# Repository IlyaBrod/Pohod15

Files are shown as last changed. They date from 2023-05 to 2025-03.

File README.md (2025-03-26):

<div align="center">
<table border="0">
 <tr>
    <td><h1> Pohod15Leg </h1>
    CAD views of the Pohod15 bio-inspired leg. (1) DC motor (2) Angle (3) Force sensor (4) Worm gear (5) Spur gear (6) Control circuit (7) Silicone tip.<br><br>  
      <div align="center">
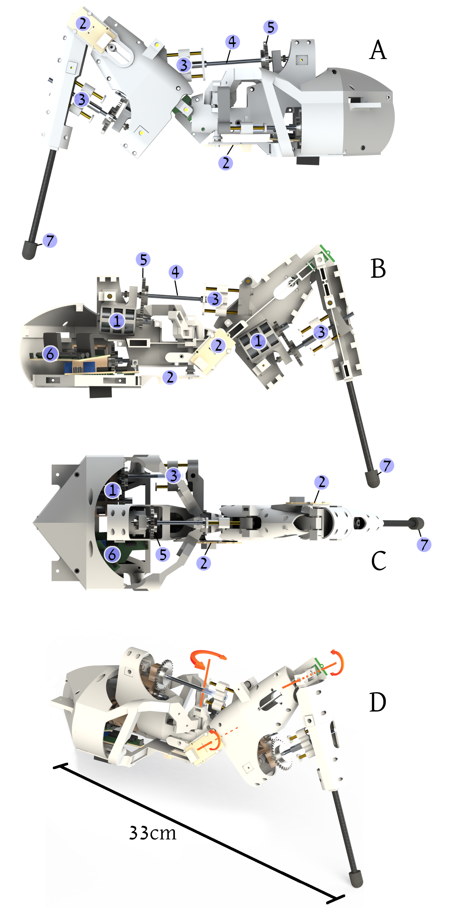
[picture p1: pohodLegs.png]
      
    </div>
    </td>
    <td>
    <h1> Description: </h1>
    This project presents the design of a 3 DoF bio-inspired robotic leg. The desert ant <i>Cataglyphis fortis</i> was used as a reference for segment sizing, with a scale ratio of 1:30.<br><br>
The structure is mainly composed of FDM 3D-printed parts. An additional carbon fiber shaft is used for the tibia, and a silicone molded tip improves surface adherence.<br>  
The actuation system consists of 3 DC motors (MABUCHI RK-370CC-14230), controlled with a custom-built shield made of L298N. However, nowadays, there are good Pololu control boards available (<a href="https://www.pololu.com/category/10/brushed-dc-motor-controllers">Pololu control boards</a>).<br>  
An irreversible worm-gear system is built using custom-machined axes jointed to Delrin spur gears to double the motor's torque output. These parts can also be assembled from cut threaded rods.<br>  
Angular sensors are based on the AS5600 from AMS OSRAM manufacturer. <br><br>
    <h1>  Files: </h1>
    <h3>./Pohod15ExoC</h3>
              CAD assembly files for Solidworks. An aditional .STEP model is provided.
    <h3>./ActuatorControl</h3>
              Provide the STM32 code, for actuator position control, 3DoF leg inverse kinematics and trajectory generation.  <br><br>
              The projet was configured using STM32CubeMX software (NUCLEO STM32F411RE setup). We suggest to use STM32Studio for the code developpment.   
    <h3>./Joint sizing  </h3> 
              Provide a graphical software to choose manually the optimum size of the irreversible joint, depending the desired output torque.
    </td>
 </tr>
</table>
</div>
  
## Want to learn more about hexapod robotics?  
- Brodoline, I., Sauvageot, E., Viollet, S., Serres J. R., Shaping the energy curves of a servomotor-based hexapod robot. Sci Rep 14, 11675 (2024).
  <a href="https://doi.org/10.1038/s41598-024-62184-y">https://www.nature.com/articles/s41598-024-62184-y</a>
- Manoonpong P, Patanè L, Xiong X, Brodoline I, Dupeyroux J, Viollet S, Arena P, Serres JR. Insect-Inspired Robots: Bridging Biological and Artificial Systems. Sensors. 2021; 21(22):7609.
<a href="https://www.mdpi.com/1424-8220/21/22/7609">https://doi.org/10.3390/s21227609</a>

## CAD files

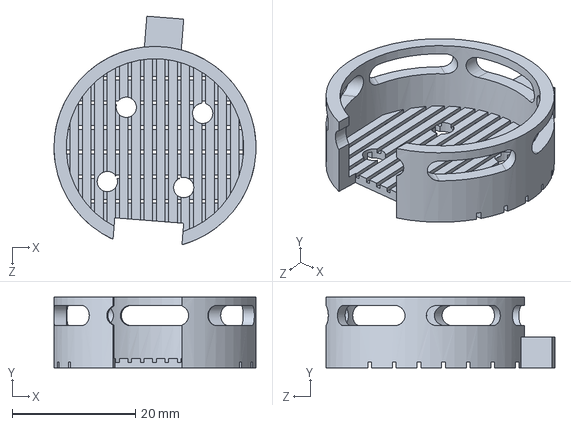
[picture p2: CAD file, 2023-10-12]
Pohod15ExoC/electronics/motor_IQ_attach.SLDPRT
32.7 x 11.5 x 37.1 mm

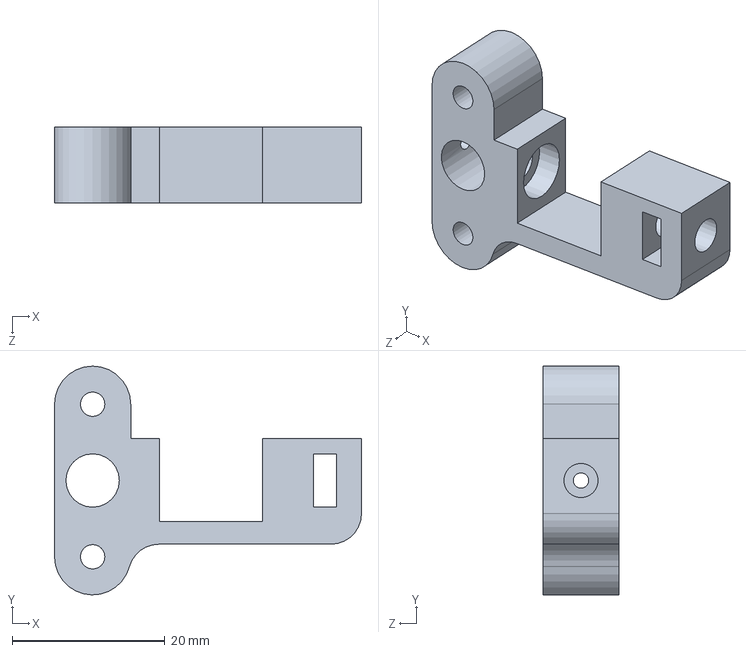
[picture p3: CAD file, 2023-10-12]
Pohod15ExoC/force sensor/forceSensor_Joint_torax.SLDPRT
40.2 x 30.0 x 10.0 mm

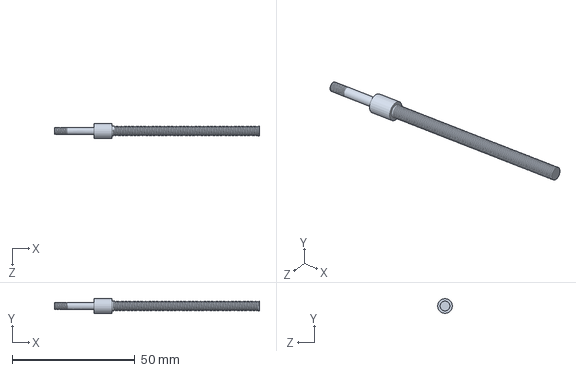
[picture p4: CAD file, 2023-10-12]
Pohod15ExoC/gears/Tibia_wormGearM4.SLDPRT
83.5 x 6.00 x 6.00 mm

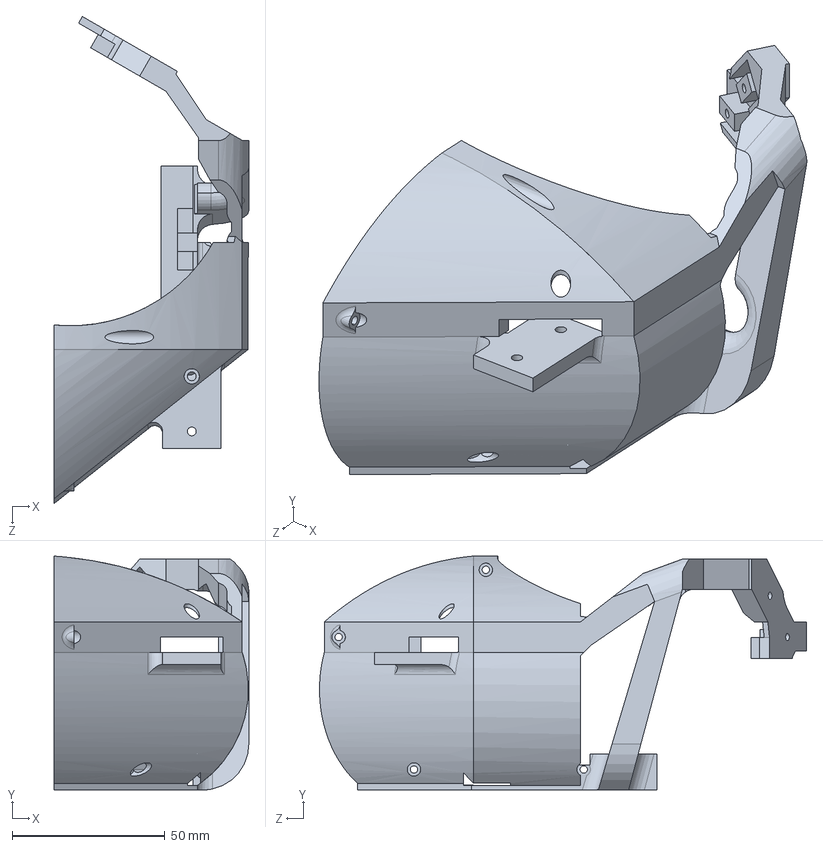
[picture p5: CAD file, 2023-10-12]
Pohod15ExoC/main parts/Symétrietorax_cuticule_R.SLDPRT
63.7 x 76.5 x 159.3 mm

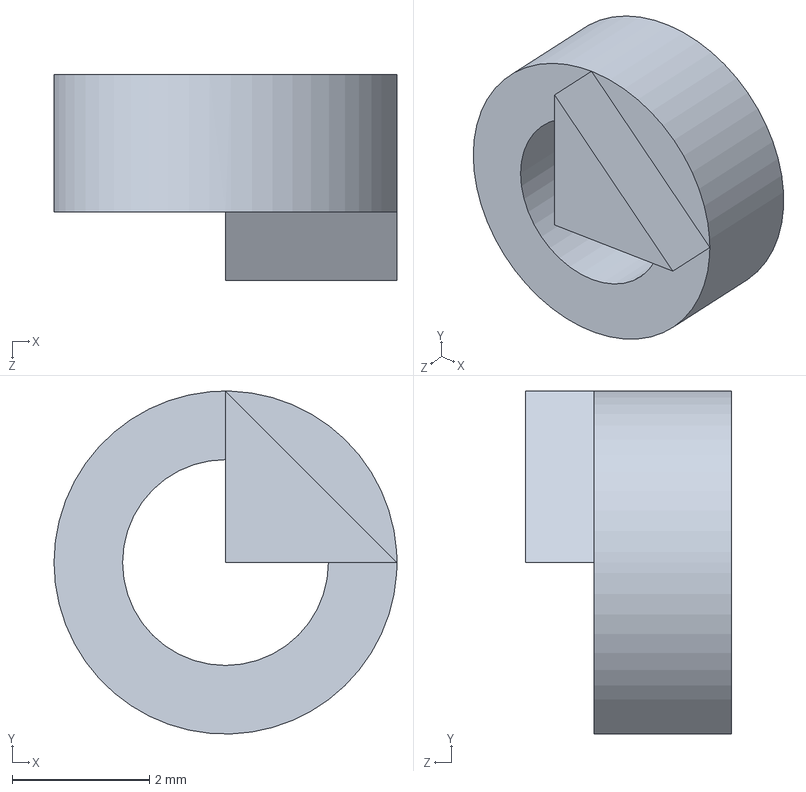
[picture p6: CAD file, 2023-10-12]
Pohod15ExoC/referenceCircle.SLDPRT
5.00 x 5.00 x 3.00 mm

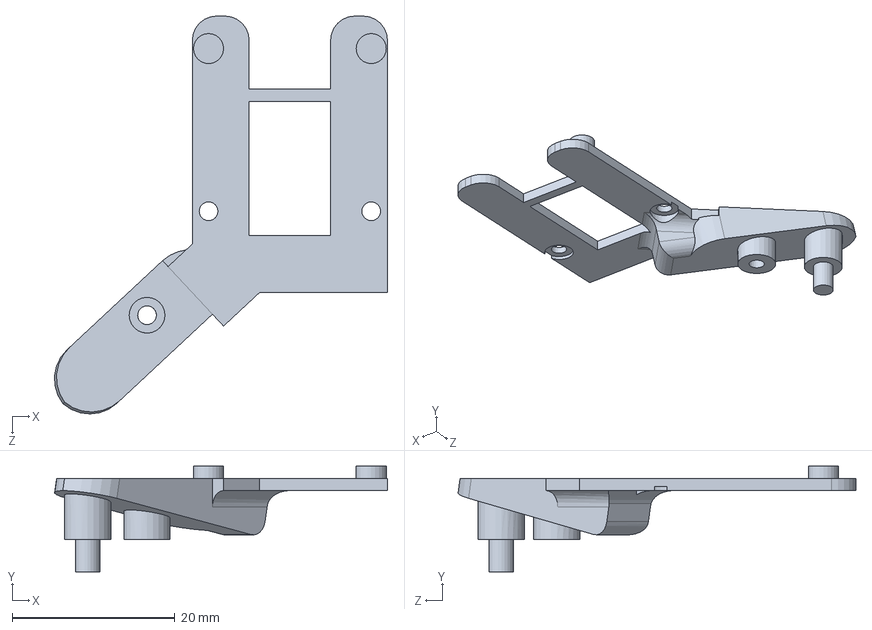
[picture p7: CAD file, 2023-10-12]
Pohod15ExoC/electronics/AS5600sensor_support_coxa.SLDPRT
40.9 x 13.0 x 48.9 mm

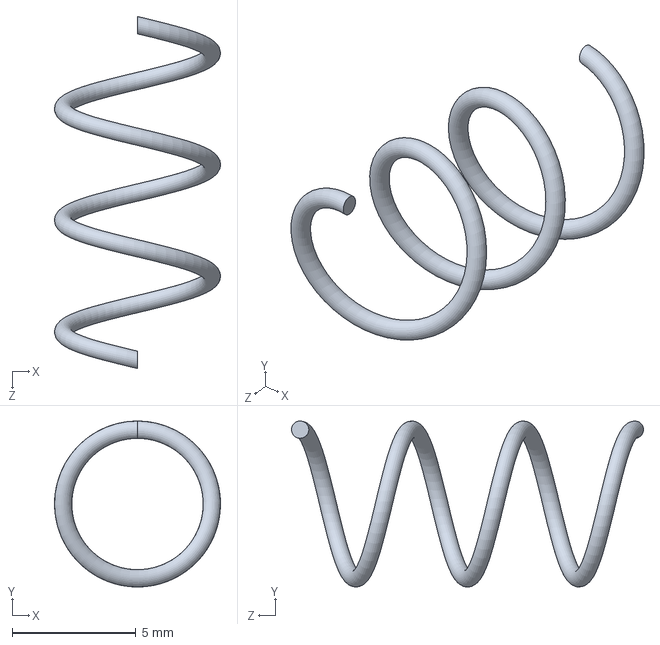
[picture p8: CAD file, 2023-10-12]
Pohod15ExoC/force sensor/forceSensor_spring.SLDPRT
6.70 x 6.70 x 14.2 mm

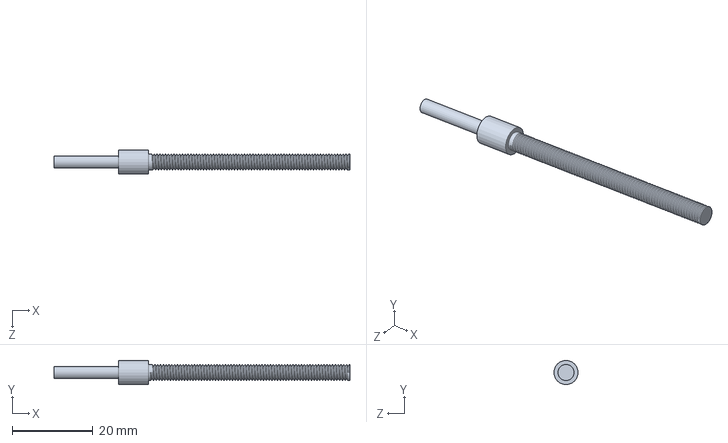
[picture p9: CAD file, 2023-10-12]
Pohod15ExoC/gears/Femur_wormGearM4.SLDPRT
73.5 x 6.00 x 6.00 mm

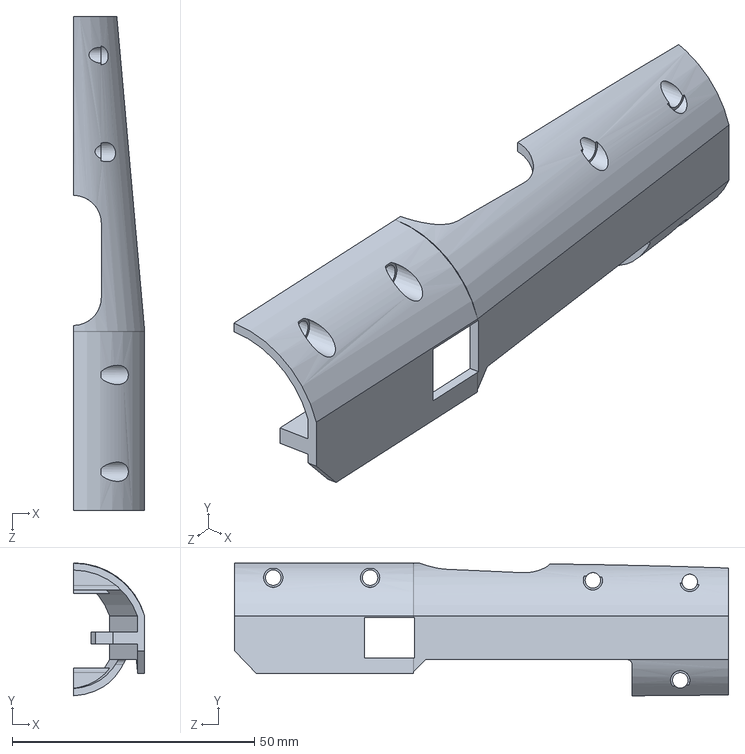
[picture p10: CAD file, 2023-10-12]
Pohod15ExoC/main parts/Symétrietibia_cuticule_R.SLDPRT
14.8 x 27.4 x 102.0 mm

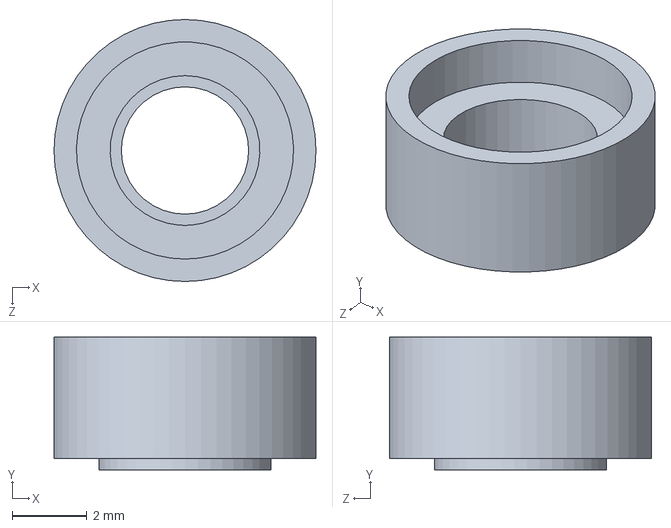
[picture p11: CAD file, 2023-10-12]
Pohod15ExoC/electronics/motor_entretoise.SLDPRT
7.00 x 3.55 x 7.00 mm

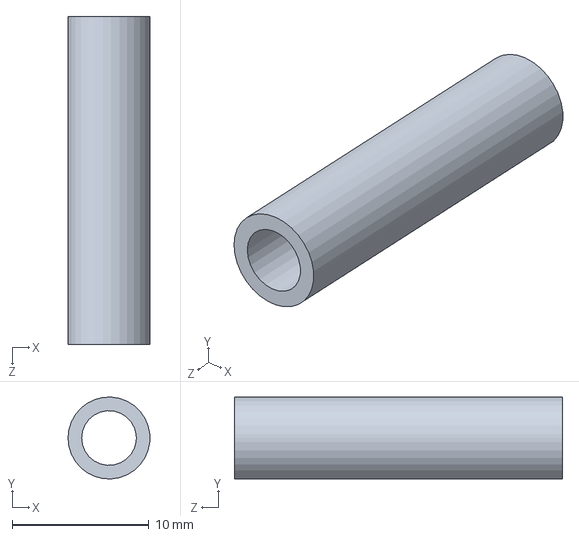
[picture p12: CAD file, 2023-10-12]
Pohod15ExoC/force sensor/forceSensor_gear.SLDPRT
6.00 x 5.99 x 24.0 mm

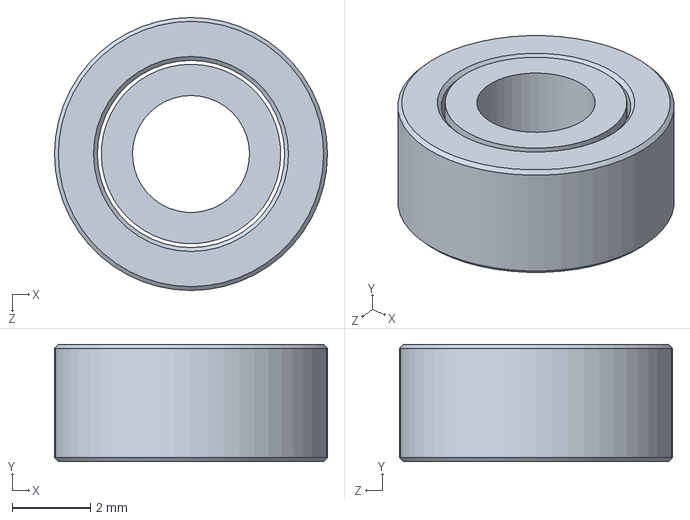
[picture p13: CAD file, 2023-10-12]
Pohod15ExoC/gears/bearing_MR63ZZ.SLDPRT
7.00 x 3.00 x 7.00 mm

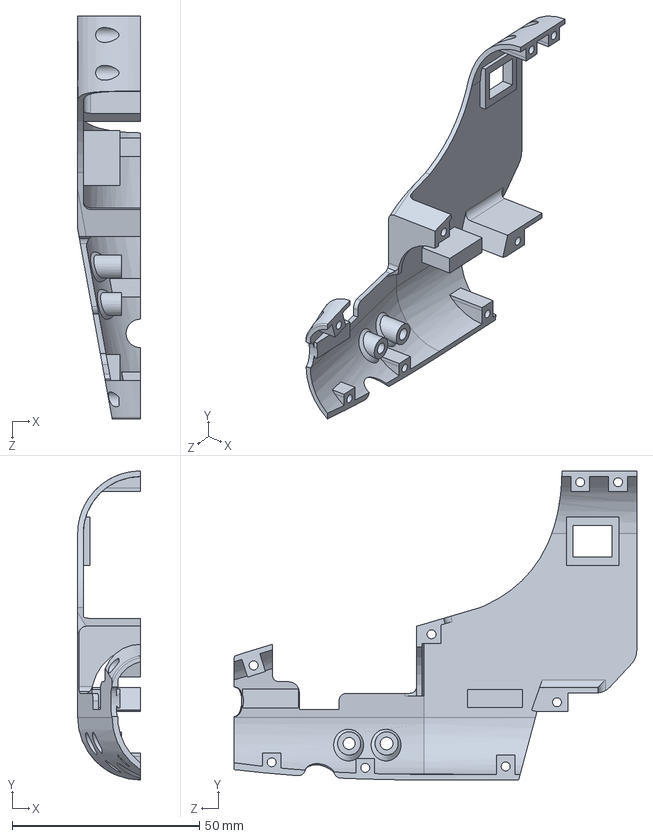
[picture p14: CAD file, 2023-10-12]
Pohod15ExoC/main parts/coxa_cuticule_R.SLDPRT
16.8 x 82.5 x 107.5 mm

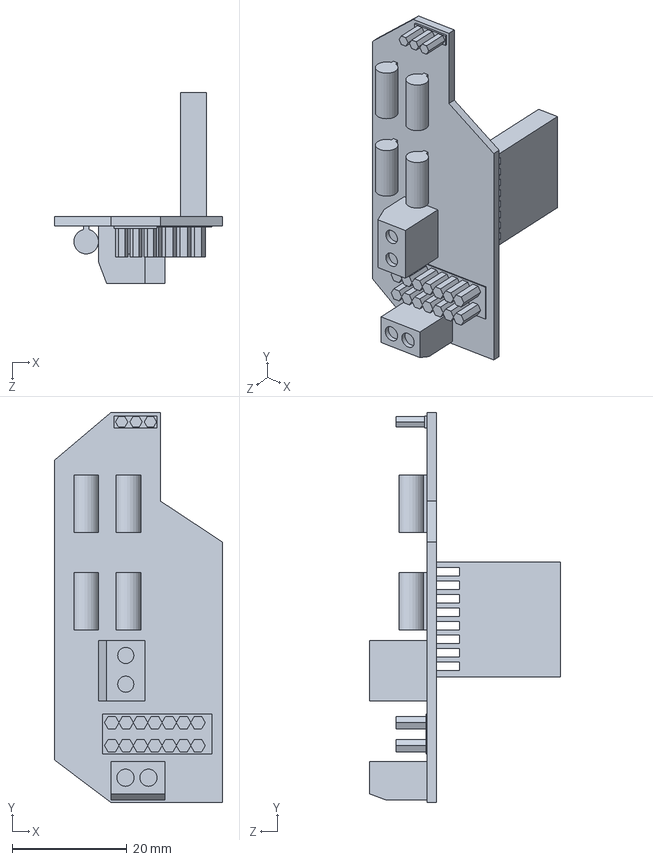
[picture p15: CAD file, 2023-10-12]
Pohod15ExoC/electronics/PCB_1M.SLDPRT
29.2 x 67.8 x 33.2 mm

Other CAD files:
Pohod15ExoC/force sensor/forceSensor_bearing.SLDPRT
Pohod15ExoC/gears/Coxa_wormGearM4.SLDPRT
Pohod15ExoC/main parts/torax_motorFix.SLDPRT
Pohod15ExoC/electronics/PCB_M2.SLDPRT
Pohod15ExoC/electronics/AS51sensor.SLDPRT
Pohod15ExoC/electronics/AS5600sensor.SLDPRT
Pohod15ExoC/electronics/AS5600sensor_support_base.SLDPRT
Pohod15ExoC/electronics/AS5600sensor_support_femur.SLDPRT
Pohod15ExoC/electronics/AS5600sensor_support_torso.SLDPRT
Pohod15ExoC/electronics/magnet.SLDPRT
Pohod15ExoC/electronics/magnetCentrer.SLDPRT
Pohod15ExoC/electronics/magnet_support_coxa.SLDPRT
Pohod15ExoC/electronics/motor_mabushi.SLDPRT
Pohod15ExoC/electronics/motor_mabushi_attach.SLDPRT
Pohod15ExoC/force sensor/forceSensor_Axe.SLDPRT
Pohod15ExoC/force sensor/forceSensor_Joint_tibia.SLDPRT
Pohod15ExoC/force sensor/forceSensor_Stop.SLDPRT
Pohod15ExoC/force sensor/forceSensor_slider.SLDPRT
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

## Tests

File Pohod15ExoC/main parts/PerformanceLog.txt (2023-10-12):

Mesh Preparation:  0 hr 0 min 0 sec
Copying bodies to mesh:  0 hr 0 min 0 sec
CB Mesh surface mesh:  0 hr 0 min 1 sec
CB Mesh volume mesh:  0 hr 0 min 0 sec
CB Mesh arrange mesh data:  0 hr 0 min 0 sec
Beam mesh:  0 hr 0 min 0 sec
Preparing to transfer data:  0 hr 0 min 1 sec
Processing material properties:  0 hr 0 min 0 sec
Processing element groups:  0 hr 0 min 0 sec
Processing drop test gap nodes:  0 hr 0 min 0 sec
Updating thickness for shell regions:  0 hr 0 min 0 sec
Processing rconst for elements:  0 hr 0 min 0 sec
Processing egroups:  0 hr 0 min 0 sec
Transferring loads and boundary conditions:  0 hr 0 min 0 sec
Generating body pairs to check contact:  0 hr 0 min 0 sec
Generating contacts:  0 hr 0 min 0 sec
Number of Contacts: 0
Transfer SL1 data:  0 hr 0 min 0 sec
Generate more accurate contact data:  0 hr 0 min 0 sec
Number of contact data: 0
Transfer beam/joint contact data:  0 hr 0 min 0 sec
Transferring other special loads:  0 hr 0 min 0 sec
Transferring bearing loads:  0 hr 0 min 0 sec
Transferring mass elements:  0 hr 0 min 0 sec
Transferring point loads:  0 hr 0 min 0 sec
Transferring distributed beam loads:  0 hr 0 min 0 sec
Transferring rigid bodies:  0 hr 0 min 0 sec
Transferring component no penetration:  0 hr 0 min 0 sec
Writing Data:  0 hr 0 min 0 sec
Transferring analysis options:  0 hr 0 min 0 sec
Total midsurf mapping:  0 hr 0 min 0 sec

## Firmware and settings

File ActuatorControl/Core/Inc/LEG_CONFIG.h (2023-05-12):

/**
	*	Functions to control Pohod Legs
	*
	*
	*							 J1						O  o					J1'
	*							/   \				|	BODY |			/			\
	*						/				J2---J3			J3'---J2'				\
	*				   V 																		 V
	*/

#ifndef LEG_CONFIG
#define LEG_CONFIG

//#################################################		GENERAL
#define PI (float)(3.14159265359f)
#define MAX(a,b) (((a)>(b))?(a):(b))
#define MIN(a,b) (((a)<(b))?(a):(b))
#define RAD2DEG(a) ((a)*180.0/PI)
#define DEG2RAD(a) ((a)*PI/180.0)


//#################################################		DEBUG ON/OFF
//Uncomment to debug
//#define DEBUG_SPEED
#define DEBUG_ANGLE_DEG
//#define DEBUG_TECH
#define DEBUG_SAVE_IO

//#################################################		CONTROL DESIGN
#define DEFAULT_STEP_LENGTH 100 //[mm]
#define DEFAULT_STEP_HIGH 100 //[mm]
#define DEFAULT_STEP_HIGH_OFFSET 50 //[mm]
#define DEFAULT_STEP_DIST 330 //[mm] Distance from the leg fixation to the tip along x
#define DEFAULT_FREQ 1 //[Hz]

#define FILTER_NB 3//Control filter order (numerator)
#define FILTER_NA 3//Control filter order (denominator)
#define FILTER_N ((FILTER_NB <= FILTER_NA) ? FILTER_NA : FILTER_NB)

#define CMD_N 80 //Number of points in the command

#define ROBOT_VOLTAGE (double)(12.0) //Volts
#define VOLT_TO_PWM (double)((double)(PWM_PERIOD)/ROBOT_VOLTAGE)

//#################################################		JOINTS PARAMS

#define JOINT1
#define JOINT2
#define JOINT3

#define ID1	0
#define ID2	1
#define ID3	2

//Minimal and maximal angles definition [unit: sensor ticks]
#define ID1_AGL_MIN (uint16_t)865
#define ID1_AGL_MAX (uint16_t)1529
#define ID2_AGL_MIN (uint16_t)250
#define ID2_AGL_MAX (uint16_t)805
#define ID3_AGL_MIN (uint16_t)523
#define ID3_AGL_MAX (uint16_t)1049

#define ID1_DEFAULT_ANGLE (ID1_AGL_MAX - ID1_AGL_MIN)/2 //[] reset angle of each joint
#define ID2_DEFAULT_ANGLE (ID2_AGL_MAX - ID2_AGL_MIN)/2 //[]
#define ID3_DEFAULT_ANGLE (ID3_AGL_MAX - ID3_AGL_MIN)/2 //[]

//Clockwise - counter clockwise rotation setting [0;1]
#define ID1_POLARITY 1
#define ID2_POLARITY 0
#define ID3_POLARITY 0

#define ERROR_BEFORE_WAIT 0.017f //in rads
	
//Geometric DATA
//Distances between joints
#define L_TIBIA 206 //[mm]
#define L_FEMUR 117 //[mm]
#define L_COXA 27 //[mm]
#define L_TORAX 134 //[mm]

#define OFFSET_ANGLE (float)(36.0f) //Leg y axis angle offset




#endif

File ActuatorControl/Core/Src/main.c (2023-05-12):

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
/* Includes ------------------------------------------------------------------*/
#include "main.h"

/* USER CODE BEGIN Includes */
#include "Command/legController.h"
//#include "Motion/motion.h"
#include "Motion/motion.h"
#include "customVars.h"
//#include "../../PWM_control.h"
/* USER CODE END Includes */

ADC_HandleTypeDef hadc1;
I2C_HandleTypeDef hi2c2;
TIM_HandleTypeDef htim1;
TIM_HandleTypeDef htim11;
UART_HandleTypeDef huart2;

/* USER CODE BEGIN PV */
uint8_t UARTbuffer[3] = {0}; //command reception buffer
uint8_t UARTspeed = 0; //received speed value

float time = 0;
float freq = DEFAULT_FREQ;
float cmd[3] = {ID1_DEFAULT_ANGLE,ID2_DEFAULT_ANGLE,ID3_DEFAULT_ANGLE};

/* USER CODE END PV */

void SystemClock_Config(void);
static void MX_GPIO_Init(void);
static void MX_ADC1_Init(void);
static void MX_TIM1_Init(void);
static void MX_TIM11_Init(void);
static void MX_I2C2_Init(void);
static void MX_USART2_UART_Init(void);
/**
  * @brief  The application entry point.
  * @retval int
  */
int main(void)
{
  /* USER CODE BEGIN 1 */
	/* PWM TEST
		pwm_write(&htim1,TIM_CHANNEL_1,840);
		HAL_Delay(1000);
		pwm_write(&htim1,TIM_CHANNEL_1,0);
		HAL_Delay(1000);
			 END PWM TEST*/
  /* USER CODE END 1 */

  /* MCU Configuration--------------------------------------------------------*/

  /* Reset of all peripherals, Initializes the Flash interface and the Systick. */
  HAL_Init();

  /* Configure the system clock */
  SystemClock_Config();

  /* Initialize all configured peripherals */
  MX_GPIO_Init();
  MX_ADC1_Init();
  MX_TIM1_Init();
  MX_TIM11_Init();
  MX_I2C2_Init();
  MX_USART2_UART_Init();
  /* USER CODE BEGIN 2 */
	
  //Leg PATH
  	//uint16_t j1_cmd[CMD_N] = {1425,1423,1420,1418,1416,1415,1413,1411,1409,1408,1406,1405,1404,1402,1401,1400,1399,1398,1397,1396,1396,1395,1394,1394,1393,1393,1393,1393,1393,1393,1393,1393,1393,1393,1393,1394,1394,1395,1396,1396,1397,1398,1399,1400,1401,1402,1404,1405,1406,1408,1409,1411,1413,1415,1416,1418,1420,1423,1425,1427,1332,1270,1239,1236,1261,1250,1241,1235,1231,1230,1231,1235,1241,1250,1261,1236,1239,1270,1332,1427};
  	//uint16_t j2_cmd[CMD_N] = {283,284,285,286,287,289,290,290,291,292,293,294,295,295,296,297,297,298,298,299,299,300,300,300,300,301,301,301,301,301,301,301,301,301,300,300,300,300,299,299,298,298,297,297,296,295,295,294,293,292,291,290,290,289,287,286,285,284,283,281,417,536,638,721,783,792,799,804,807,808,807,804,799,792,783,721,638,536,417,281};
  	//uint16_t j3_cmd[CMD_N] = {911,907,903,900,896,892,888,885,881,877,873,869,865,862,858,854,850,846,842,839,835,831,827,823,819,815,812,808,804,800,796,792,788,785,781,777,773,769,765,761,758,754,750,746,742,738,735,731,727,723,719,715,712,708,704,700,697,693,689,685,685,685,685,685,685,707,730,753,777,800,823,847,870,893,915,915,915,915,915,915};

  //Controller parameters
	
	double j1_b[FILTER_NB+1] = {0,0.000389180566340473,2.20217651193603e-05,-0.000367158801221113};
	double j1_a[FILTER_NA+1] = {1,-2.86108563590668,2.72699391536802,-0.865908394532816};

	double j2_b[FILTER_NB+1] = {0};
	double j2_a[FILTER_NA+1] = {0};
	
	double j3_b[FILTER_NB+1] = {0};
	double j3_a[FILTER_NA+1] = {0};

	uint8_t scenario = 0;
	uint16_t wstep = 0; //number of steps to do
	bool start = false; //start the walking
	uint32_t tic = 0;
	uint32_t toc = 0;
	LegInit(&htim1,&hi2c2,&htim11);
	LegSetupController(j1_b,j1_a,j2_b,j2_a,j3_b,j3_a); //Save control parameters
	//JointDisable(ID1);
	JointDisable(ID2);
	JointDisable(ID3);
	

	HAL_Delay(1000); //Little delay for suspens
	
	//SETUP CODE
	LegReset();
	LegControllerStart();
	HAL_Delay(5000);
	
  /* USER CODE END 2 */

  /* Infinite loop */
  /* USER CODE BEGIN WHILE */
	/* CODE SYSTEM IDENTIFICATION
	LegSet(ID1,ID1_AGL_MIN+20);
	HAL_Delay(10000);
	//DEBUG_ioStart();
	HAL_Delay(200);
	LegSet(ID1,ID1_AGL_MAX-20);
	HAL_Delay(700);
	LegSet(ID1,ID1_AGL_MIN+20);
	HAL_Delay(700);
	LegSet(ID1,(ID1_AGL_MIN+ID1_AGL_MAX)/2);
	HAL_Delay(800);
	LegReset();
	CODE SYSTEM IDENTIFICATION END*/

	//Motion planning
	motion_init();



	while (1)
{

		tic = HAL_GetTick();
		//USART COMMANDS
		/*HAL_UART_Receive(&huart2,UARTbuffer,3,20);

		if(UARTbuffer[0] == 'S') {
		      //Commands interpret
		      //Power on
		      if(UARTbuffer[1]=='P') {
		    	  UARTspeed = UARTbuffer[2];
		    	  //motion_set_f(value*MAX_SPEED/100);
		    	  } //change frequency (speed)
		      else if(UARTbuffer[1]=='E') {   //scenario selection
		        scenario = UARTbuffer[2];
		        switch(scenario) {
		         case 0:
		           wstep = 0;
		           break;
		         case 1:
		           start=true;
		           wstep = 1;
		           break;
		         case 2:
		           start=true;
		           break;
		         case 3:
		           start=true;
		           break;
		        }
		      }
		    }*/

		  UARTbuffer[0] = '0';
		  UARTbuffer[1] = '0';
		  UARTspeed = 0;
		  UARTspeed = 10;
		  start = true;
		  wstep = 1;

		  //MOTION control
		  if(start == true && UARTspeed>0) {
			tic = HAL_GetTick();
			time = time + freq*0.02; //increment time from 0 to 1 by time step
			if (time > 1.0) {
			  time = time - 1.0;
			}

			if(wstep==0) {time=0;start=false;}
			motion_get(time, cmd);

			//Set command
			LegSet(ID1,(uint16_t)(cmd[ID1]/ANGLE_SENSIVITY_RAD));
			LegSet(ID2,(uint16_t)(cmd[ID2]/ANGLE_SENSIVITY_RAD));
			LegSet(ID3,(uint16_t)(cmd[ID3]/ANGLE_SENSIVITY_RAD));

			//50Hz loop
			toc = 20-HAL_GetTick()-tic;
			if(toc>0) {
			  HAL_Delay(toc);
			}
		 }


		/* Old code
		for(int i=0;i<CMD_N;i++) {
			//LegSetAllWait(j1_cmd[i],j2_cmd[i],j3_cmd[i]);
			//LegSetWait(ID1,j1_cmd[i]);
			LegSet(ID1,j1_cmd[i]);
			LegSet(ID2,j2_cmd[i]);
			LegSet(ID3,j3_cmd[i]);
			HAL_Delay(20);

		}*/
		//HAL_Delay(20);

    /* USER CODE END WHILE */

    /* USER CODE BEGIN 3 */
  }
  /* USER CODE END 3 */
}

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


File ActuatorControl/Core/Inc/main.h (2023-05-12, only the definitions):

#define B1_Pin GPIO_PIN_13
#define B1_GPIO_Port GPIOC
#define CURR_1_Pin GPIO_PIN_0
#define CURR_1_GPIO_Port GPIOA
#define CURR_2_Pin GPIO_PIN_1
#define CURR_2_GPIO_Port GPIOA
#define USART_TX_Pin GPIO_PIN_2
#define USART_TX_GPIO_Port GPIOA
#define USART_RX_Pin GPIO_PIN_3
#define USART_RX_GPIO_Port GPIOA
#define CURR_3_Pin GPIO_PIN_4
#define CURR_3_GPIO_Port GPIOA
#define LD2_Pin GPIO_PIN_5
#define LD2_GPIO_Port GPIOA
#define SSI_CS_Pin GPIO_PIN_7
#define SSI_CS_GPIO_Port GPIOA
#define M2_IN2_Pin GPIO_PIN_6
#define M2_IN2_GPIO_Port GPIOC
#define M1_IN2_Pin GPIO_PIN_7
#define M1_IN2_GPIO_Port GPIOC
#define M2_IN1_Pin GPIO_PIN_8
#define M2_IN1_GPIO_Port GPIOC
#define M1_PWM_Pin GPIO_PIN_8
#define M1_PWM_GPIO_Port GPIOA
#define M2_PWM_Pin GPIO_PIN_9
#define M2_PWM_GPIO_Port GPIOA
#define M3_PWM_Pin GPIO_PIN_10
#define M3_PWM_GPIO_Port GPIOA
#define TMS_Pin GPIO_PIN_13
#define TMS_GPIO_Port GPIOA
#define TCK_Pin GPIO_PIN_14
#define TCK_GPIO_Port GPIOA
#define M3_IN2_Pin GPIO_PIN_4
#define M3_IN2_GPIO_Port GPIOB
#define M3_IN1_Pin GPIO_PIN_5
#define M3_IN1_GPIO_Port GPIOB
#define M1_IN1_Pin GPIO_PIN_6
#define M1_IN1_GPIO_Port GPIOB

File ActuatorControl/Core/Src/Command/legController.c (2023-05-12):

#include "legController.h"

#ifdef DEBUG_SAVE_IO
uint16_t input_save[1000] = {0};
uint16_t output_save[1000] = {0};
int cmd_save[1000] = {0};
uint16_t index_save = 0;
uint8_t io_start = 0;
#endif

CONTROLLER Leg = {0};
JOINT jnt1;
JOINT jnt2;
JOINT jnt3;
//int sysclk_period =0;

uint16_t AGL_LIMITS[6] = {ID1_AGL_MIN,ID2_AGL_MIN,ID3_AGL_MIN,
						  ID1_AGL_MAX,ID2_AGL_MAX,ID3_AGL_MAX};

uint16_t seuil(uint8_t ID, uint16_t val); //Limits angles values to extremes
void zeros(float * memory,unsigned int size); //Init array to zeros			
void Delay_ns(unsigned int delay);														

														//Init Settings
void LegInit(TIM_HandleTypeDef *htimPWM, I2C_HandleTypeDef *hi2c, TIM_HandleTypeDef *htimINT)
{
	//Clock period calculation
	//int sysclk = HAL_RCC_GetSysClockFreq();
	//float period = ((float)1)/((float)sysclk);
	//period = period*1000000000;
	//sysclk_period = (int)(period);
	
	
	Leg.joints[0] = &jnt1;
	Leg.joints[1] = &jnt2;
	Leg.joints[2] = &jnt3;
	
	Leg.joints[0]->ENABLE = 0;
	Leg.joints[1]->ENABLE = 0;
	Leg.joints[2]->ENABLE = 0;
	
	#ifdef JOINT1
	Leg.joints[0]->ID = ID1;
	Leg.joints[0]->DIR = ID1_POLARITY;
	Leg.joints[0]->pwmTim = htimPWM;
	Leg.joints[0]->TARGET = AGL_LIMITS[ID1];
	Leg.joints[0]->pwmChannel = TIM_CHANNEL_1;
	Leg.joints[0]->hi2c = hi2c;
	jointInit(Leg.joints[0]);
	#endif
	
	#ifdef JOINT2
	Leg.joints[1]->ID = ID2;
	Leg.joints[1]->DIR = ID2_POLARITY;
	Leg.joints[1]->pwmTim = htimPWM;
	Leg.joints[1]->TARGET = AGL_LIMITS[ID2];
	Leg.joints[1]->pwmChannel = TIM_CHANNEL_2;
	Leg.joints[1]->hi2c = hi2c;
	jointInit(Leg.joints[1]);
	#endif
	
	#ifdef JOINT3
	Leg.joints[2]->ID = ID3;
	Leg.joints[2]->DIR = ID3_POLARITY;
	Leg.joints[2]->pwmTim = htimPWM;
	Leg.joints[2]->TARGET = AGL_LIMITS[ID3];
	Leg.joints[2]->pwmChannel = TIM_CHANNEL_3;
	Leg.joints[2]->hi2c = hi2c;
	jointInit(Leg.joints[2]);
	#endif
	
	
	//Init controller parameters
	for(int i=0;i<3;i++) {
		for(int j=0;j<=FILTER_NA;j++) {
			Leg.a[i][j] = 0;
		}
	}
	
	for(int i=0;i<3;i++) {
		for(int j=0;j<=FILTER_NB;j++) {
			Leg.b[i][j] = 0;
		}
	}
	
		for(int i=0;i<3;i++) {
		for(int j=0;j<=FILTER_N;j++) {
			Leg.w[i][j] = 0;
		}
	}
	
	zeros(Leg.speed_memory,3);
	zeros(Leg.pos_memory,3);
	
	//Start interruption on TIMER
	Leg.htim = htimINT;
	
}

void LegControllerStart(void)
{
		HAL_TIM_Base_Start_IT(Leg.htim);
}

void LegControllerStop(void)
{
	HAL_TIM_Base_Stop_IT(Leg.htim);
}

void LegSetupController(double j1b[FILTER_NB+1],double j1a[FILTER_NA+1],double j2b[FILTER_NB+1],double j2a[FILTER_NA+1],double j3b[FILTER_NB+1],double j3a[FILTER_NA+1])
{
	for(int i =0;i<=FILTER_NB;i++){
		Leg.b[0][i] = j1b[i];
	}
	
	for(int i =0;i<=FILTER_NA;i++){
		Leg.a[0][i] = j1a[i];
	}
	
	for(int i =0;i<=FILTER_NB;i++){
		Leg.b[1][i] = j2b[i];
	}
	
	for(int i =0;i<=FILTER_NA;i++){
		Leg.a[1][i] = j2a[i];
	}
	
		for(int i =0;i<=FILTER_NB;i++){
		Leg.b[2][i] = j3b[i];
	}
	
	for(int i =0;i<=FILTER_NA;i++){
		Leg.a[2][i] = j3a[i];
	}


}

//#################################################### LEG USER FUNCTIONS

void LegReset(void)
{
	
	for(int i=0;i<3;i++)
	{
		if(Leg.joints[i]->ENABLE==1) {
			Leg.joints[i]->TARGET = (AGL_LIMITS[i+3]-AGL_LIMITS[i])/2+AGL_LIMITS[i];
		}
	}
}

void LegSet(uint8_t ID, uint16_t POS){
	
	Leg.joints[ID]->TARGET = seuil(ID,POS);
}

void LegSetAll(uint16_t POS1, uint16_t POS2,uint16_t POS3)
{
	LegSet(ID1,POS1);
	LegSet(ID2,POS2);
	LegSet(ID3,POS3);
}

void LegSetWait(uint8_t ID, uint16_t POS)
{
	LegSet(ID,POS);
	while(Leg.joints[ID]->ERR>ERROR_BEFORE_WAIT)
	{
		Delay_ns(77);
	}
}

void LegSetAllWait(uint16_t POS1,uint16_t POS2,uint16_t POS3)
{
	LegSet(ID1,POS1);
	LegSet(ID2,POS2);
	LegSet(ID3,POS3);
	
	
	while(Leg.joints[ID1]->ERR>ERROR_BEFORE_WAIT || Leg.joints[ID2]->ERR>ERROR_BEFORE_WAIT || Leg.joints[ID3]->ERR>ERROR_BEFORE_WAIT)
	{
		Delay_ns(77);
	}
	
}

void JointDisable(uint8_t ID) {

	Leg.joints[ID]->ENABLE = 0;

}
void JointEnable(uint8_t ID) {
	Leg.joints[ID]->ENABLE = 1;
}



//######################################################

// PRIVATE FUNCTION

void zeros(float * memory,unsigned int size) {

	for(int i=0;i<size;i++)
	{
		memory[i]=0;
	}
}

/*void Delay_ns(unsigned int delay)
{
	unsigned int ns =  (unsigned int)delay/sysclk_period/7;
	for(int i=0;i<=ns;i++);
}*/

uint16_t seuil(uint8_t ID, uint16_t val){
	uint16_t valS=val;
	uint16_t max = AGL_LIMITS[ID+3];
	uint16_t min = AGL_LIMITS[ID];
	
	if(val>max) valS = max;
	else if(val<min) valS = min;
	
	return valS;
}


void DEBUG_ioStart(void) {
	io_start = 1;
}

void LegUpdate(TIM_HandleTypeDef *htim)
{	
	 #ifdef DEBUG_TECH
	 uint32_t tic = HAL_GetTick();
	 #endif

	 if(__HAL_TIM_GET_FLAG(Leg.htim,TIM_FLAG_UPDATE) != RESET) {
		 
		 double ctrl=0;

		 for(int i=0; i<3;i++)
		 {
			 if(Leg.joints[i]->ENABLE == 1) {
				 
				 
				 jointPreUpdate(Leg.joints[i]); //Read sensors values


				 #ifdef DEBUG_ANGLE_DEG
				 Leg.joints[i]->ANGLE_DEG =  (float)(Leg.joints[i]->ANGLE * ANGLE_SENSIVITY_DEG);
				 #endif

				 #ifdef DEBUG_SPEED
				 float spd = ((Leg.joints[i]->ANGLE*ANGLE_SENSIVITY_DEG-Leg.pos_memory[i])/0.003f * 60.0f/360.0f);
				 Leg.joints[i]->SPEED = (Leg.speed_memory[i]+ spd)/2.0f;
				 Leg.pos_memory[i] = Leg.joints[i]->ANGLE*ANGLE_SENSIVITY_DEG;
				 Leg.speed_memory[i] = spd;
				 #endif

				 Leg.joints[i]->ERR = (float)(Leg.joints[i]->TARGET-Leg.joints[i]->ANGLE)*ANGLE_SENSIVITY_RAD;
				 Leg.joints[i]->CMD = (int)(Leg.joints[i]->ERR * (30.0f) *VOLT_TO_PWM);

				 /*
				 Leg.w[i][0] = (Leg.joints[i]->TARGET* ANGLE_SENSIVITY_RAD)- (Leg.joints[i]->ANGLE*ANGLE_SENSIVITY_RAD);		 
				 Leg.w[i][0] =  atan2(sin(Leg.w[i][0]),cos(Leg.w[i][0]));
				 Leg.joints[i]->ERR = Leg.w[i][0];
				 
				 
				 for(int k=1;k<=FILTER_NB;k++) {
					 Leg.w[i][0] -= Leg.a[i][k] * Leg.w[i][k];
				 }
				 
				 for(int k=0;k<=FILTER_NA;k++) {
					 ctrl += Leg.b[i][k] * Leg.w[i][k];
				 }
				 
				 for(int k=FILTER_N;k>=1;k--) {
					 Leg.w[i][k] = Leg.w[i][k-1];
				 }
				 
				 ctrl = -1000.1f*ctrl;
				 
				 Leg.joints[i]->CMD = (int)(ctrl*VOLT_TO_PWM);
				*/
				 //COMMAND SATURATION
				 if(Leg.joints[i]->CMD>PWM_PERIOD) {
					 Leg.joints[i]->CMD = PWM_PERIOD;
				 }
				 else if(Leg.joints[i]->CMD<-PWM_PERIOD) {
					 Leg.joints[i]->CMD = -PWM_PERIOD;
				 }
				 
				 jointPostUpdate(Leg.joints[i]); //Update motor direction and command

				 #ifdef DEBUG_SAVE_IO
				 if(index_save<1000 && io_start==1) {
					 input_save[index_save] = Leg.joints[i]->TARGET;
				 	 output_save[index_save] = Leg.joints[i]->ANGLE;
				 	 cmd_save[index_save] = Leg.joints[i]->CMD;
				 	 index_save = index_save +1;
				 }
				 #endif
			 }
     }

		 
		 
		 #ifdef DEBUG_TECH
		 uint32_t toc = HAL_GetTick();
		 Leg.Tech = (float)(toc-tic);
		 Leg.Tech = ((float)(HAL_RCC_GetSysClockFreq()));
		 #endif
	 }
}

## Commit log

2023-07-05 Add joint sizing custom software
2023-10-12 Add 3D model files
    [AS51sensor.SLDPRT, AS5600sensor.SLDPRT, AS5600sensor_support_base.SLDPRT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]
2025-03-25 Add leg 3D model.

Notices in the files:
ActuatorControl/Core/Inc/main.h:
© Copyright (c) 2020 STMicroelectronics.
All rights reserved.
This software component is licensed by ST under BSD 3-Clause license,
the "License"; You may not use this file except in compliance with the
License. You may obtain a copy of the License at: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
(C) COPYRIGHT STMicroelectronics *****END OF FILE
